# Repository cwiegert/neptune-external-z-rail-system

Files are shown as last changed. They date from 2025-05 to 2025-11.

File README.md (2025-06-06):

# Neptune 4 Pro – Z Axis Linear Rail Mounting System
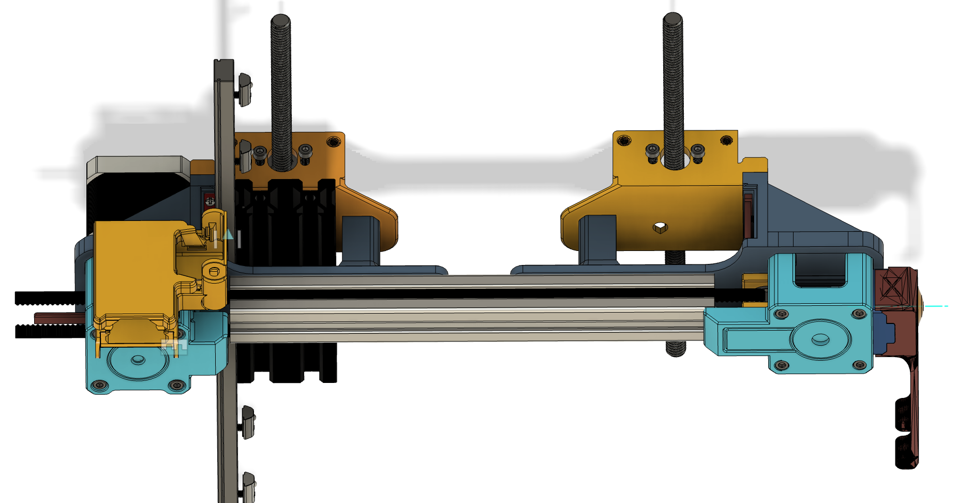
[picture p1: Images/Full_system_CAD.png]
Overview
 

This mod was inspired by the limitations and challenges imposed on Neptune printers by the TBStrong z rail kit.   Why do you need z rails at all?   Well, you don't, but I have them, and I never have to worry about aligning pom wheels, or any kind of z banding.   If you are here, you are interested in putting rails on the z axis, becuase you have probably already put the y axis rails and perhaps the x axis upgrade.    

This design incorporates rails on the outside of the Gantry.   Unlike the Tbstrong upgrade, this change will eliminate the interference with x axis movement and any cable chain system you might want to install.   The inside the gantry limits any well designed chain link system, as the adaptor off the tool head typically hits the rail on both gantry posts.

## 📦 Some basics to start wtih

- **This is an advanced mod and not something to be taking lightly.   Several different components are included in this modification and should only be done by someone with experience with complicated modifications**

- MGN12H rails are used, with the larger H carriages.

- Suggest to use light load Z rails, especially if you have a Beacon H or any other eddy probe. Any heavier preload will cause Z axis noise and cause the eddy to trigger early.

- There are prerequisites, you may want to consider. Initial release is designed to work with the SilencedFrost X axis rail upgrade  and the Layer.Shifted double shear X motor upgrade. 

- While changing the mount, consider an upgrade to a 48mm motor, over the 39mm on the stock Neptune 4 Pro.   The standard motor will work but if you are already doing this set of advanced modifications the motor upgrade is a nice add on

- All files have included in this repo which were sourced from other mods, have been modified to work for this kit.   Including the printhead hanger for the x axis rail modification and modded to support the end stop switch being flipped from stock, requireing a  finger on top of the rail to activate the end switch

- The current offset on the x axis endstop switch is designed to fit the stock position, and the finger added to the x axis printhead will trigger a stock -8.5mm
- **If you are using a tensioner idler pulley larger than a Gates Spec, be sure to print the Large profile tensioner housing**

## 🧰 Tools Required

- A working printer
- Hex drivers 2.5 and 2.0
- Soldering Iron (insert ends optional but recommended)

## 🛠️ Installation Overview

| Step | Instruction | Image |
|---|---|---|
| 1 | **Print the STL files** using your Neptune 4 Pro or another 3D printer. | |
| 2 | **Disassemble** the original Z-axis lead screw carriage if necessary. This is self-explanatory, and there are no parts from the stock Z-axis hardware that are reused except for the limit switch. | |
| 3 |  Add a M3x8 socket head screw to the rails, starting with the top and bottom, every other hole, and start a roll in t-nut to the rail |  |
| 4 |  Using the bearing keeper from the tools, remove the carraiges from the linear rail by holding the keeper tight to the rail, and slowly sliding the carriages onto the bearing keeper | |
| 5 | **Mount the linear rail** to the Z gantry. Use the `20x20x20` spacer block from the STL directory to position the 330mm rail. Tighten one rail screw, place the block on top, and align to the top of the gantry extrusion (with the top rail removed). This will give about 5mm of carriage travel before hitting the bed. Snap the MGN12H alingment tool to the bottom of the rail and align the rail to the center of the extrusion. Tighten the bottom screw tight enough to hold the rail. Move the alignment clip between the top 2 holes of the rail, loosen the top screw, snap the alignment rail to the extrusion and tighten the top screw just past finger tight.  , tighten them just past finger tight, moving the alignment jig up the rail as you go. **DO NOT ADD THE CARRIAGES YET** — you will lose bearings if you try to install the assembly all at once. | Step 3 |
| 6 | Run the belt through the tensioner pulley and set the tensioner on the x extrusion. It will register into the slides. | |
| 7 | Snap the double shear cap and the tensioner cover into the X extrusion bracket. The covers are designed to snap into the pockets on the x extrusion brackets and slide into the extrusion ends. You need to assemble the double shear bearing holder and the tensioner covers onto the x extrusion holders before assembling onto the Z rails. There will be no way to slide the ends into the 2020 extrusion once the X extrusion brackets are mounted on the 2020.  | |
| 8 | **Assemble the X-axis extrusion**. The X-axis brackets are designed for 2020 extrusion and not the stock one. The bracket mounting holes won’t align with stock extrusion holes. A future mod may support this. Using 2 M4x10 button head screws and M4 roll in t-nuts, mount the X brackets to the extrusion. Roughly align the carraige hanger portion of the bracket with the outside of the gantry rails.  Lower the assembly onto the gantry uprights, using the X-axis leveling jigs to maintain a level x axis. Leave all X extrusion screws loose for now, they will be tighten after step 7 | Step 4  Step 6|
| 9 | **Attach the carriage.** With the X extrusion in place, slide the carriages onto the rails and into the hangers. Mount them to the X-axis bracket with 4× M3x8mm flat head screws. Slide the X axis up/down a few times. Then:<br>&nbsp;&nbsp;&nbsp;&nbsp;1. Tighten the top rail screw.<br>&nbsp;&nbsp;&nbsp;&nbsp;2. Loosen other screws<br>&nbsp;&nbsp;&nbsp;&nbsp;3. Slide the X axis up and down again<br>&nbsp;&nbsp;&nbsp;&nbsp;4. Rest the X extrusion on the leveling blocks<br>&nbsp;&nbsp;&nbsp;&nbsp;5. Tighten screw nearest to X-axis on both rails<br>&nbsp;&nbsp;&nbsp;&nbsp;6. Slide the X extrusion to bottom of the rails<br>&nbsp;&nbsp;&nbsp;&nbsp;7. Tighten bottom screws<br>&nbsp;&nbsp;&nbsp;&nbsp;8. Finish by tightening remaining screws<br><br><br> At this point the carraige and the rails should be aligned and parallel to each other and the x extrusion should move freely with little to no friction |  Step 5 |
| 10 | **Tighten the X extrusion hangers**. Tighten the visible M4 screw in the X extrusion bracket using the access hole in the lead screw hanger. Remove the assembly from the gantry to access and tighten the hidden screw. Using the method described in step 4 **REMOVE THE CARRIAGES AGAIN**, repeat step 7 exactly. <br><br>Your motion system should now be aligned and level. | Step 6 |
| 11 | **Mount assembly to the lead screw nuts**. Whether using stock nuts or Oldhams, attach the lead screws. If using stock nuts: leave screws loose. If using Oldhams: tighten fully. | Step 7 |
| 12 | Slide the Printhead hanger onto the front rail. Again, you will need to upgrade to the SilencedFrost front rail hanger system, or use a top rail from the TbStrong X axis rail system to use this upgrade.  There is no adapatation to the stock Neptune 4 Pro x extrusion. Have not tested with the other Neptune 4 series. |  |
| 13 | Slide the motor into the receiver on the left side of the gantry. The motor should be difficult to slide into the receiver, and best to slide the outside into the holder, then push the back of the motor towards the linear rail carraige | |
| 14 | Follow the assembly instructions from the Layer.shifted double shear block, to mount the bearing into the holder, and the end stop into the cap of the double shear holder |  |
| 15 | Slide your belt pulley onto the belt, leave the grub nut loose.  Pressure fit the double shear pulley assembly onto the motor hanger, and add the end stop mount to the assembly by inserting the 4 screws and start them into the motor. Don't tighten them yet, just finger tight to hold the assembly together| |
| 16 |  Insert the pulley preload tool between the belt pulley and bearing of the double shear motor mount. This tool aligns the pulley with the center of the x axis extrusion and gives enough standoff to avoid rubbing on the shaft reinforcement bearing. |  |
| 17 |  Assemble the tensioner by adding the heat insert and the M3x45mm screw to the back of the tensioner | |
| 18 |  Assemble the idler pulley in the tensioner using the M5x20mm dowel. **If you are not using a Gates spec pulley, use the Large profile tensioner housing **  The tensioner slide will allow for 22mm dowel if you have 1 left over from another mod | |
| 19 | run the belt around the 2 pulleys and  making sure the tensioner pulley is onto the belt the correct way. You will need to make sure the belt is around the tensioner pulley before mounting the pulley to the cover. |  |
| 20 | Slide the tensioner into the tensioner cover, and pressure fit the tensioner cover to the x axis mount adn tighten the 4 M3x35 socket head screws  |  |
| 21 | If you are using the c270 camera holer, add the mounting block prior to adding the tensioner nob. There is no permanent mounting assembly for the block, it is loose fitting and held by the tension of the tensioner knob. The teardop around the mounting hole will register into the profile on the end of the tensioner cover. Add either the stock or the included tensioner knob and tighten slightly |  |
| 22 |  Tighten the belt to the print head hanger and assembly | |
| 23 |  Add the print head, and tune. Tension the x belt to the appropriate tension (roughly 130 HZ for sock length Neptune 4 Pro)

## 📌 Compatibility

- **Printer:** Elegoo Neptune 4 Pro, will likely work on all Neptune versions, but not tested.   If not using a X axis endstop, the Motor side double shear cover would not be needed
- **X Axis and extrusion** currently only supported on a X rail upgrade from @SilencedFrost as referenced in the BOM above
- **X Axis motor and motion**  requires the Lamarc double shear upgrade.   It may be compatible with stock limit switch and cover, but not tested
- **Rail type:** MGN12H (or similar) with 330mm recommended length.  .step files provided to invite mods for longer x extrusions and mods like purge buckets outside the print area
- **Clearances:** Designed to maintain compatibility with stock frame dimensions.  

## 🧪 Notes

- **IMPORTANT** Files are designed with **tight tolerances** to minimize backlash and reduce resonance vibrations
- .step files are included so you can modify dimensions or hole patterns as needed
- Be sure to tune your flow and PA, there are very tight tollerances designed into the parts, and there will be no design to relax the tollerances
- Supports are built in, and desinged to be break-away after cooling.   Difficult to remove supports with hot/warm part
- ASA-CF does not seem to hold up to screw pressure to well.   As the screw head puts pressure on the assembly, the ASA catestophically fails and splits the parts.   PETG-GF can be used as alternative where screw pressure causes ASA to fail
- Socket head screws used where over tightening will not cause splitting

## 📦 BOM
<small>
  
| Item| Part Description | Quantity | Source/Link | Notes |
|-----|---|---|---|---|
| 1 | MGN12H Linear Rail (330mm) | 2 | [Amazon](https://www.amazon.com/dp/B07Z5NKF42) | Light preload recommended |
| 2 | M3 x 8mm socket Head Screws | 16 | [Amazon](https://www.amazon.com/dp/B07CJ9BRCK?ref_=ppx_hzsearch_conn_dt_b_fed_asin_title_6&th=1) | required for mounting the rails and a number of the printed components |
| 3 | M3 x 6 Flat head Screws | 8 | [Amazon](https://www.amazon.com/dp/B0CG9K1NDX?ref_=ppx_hzsearch_conn_dt_b_fed_asin_title_2) | Mounting the carraiges to the X axis brackets |
| 4 | M3 x 8mm Button Head Screws | 4 | [Amazon](https://www.amazon.com/dp/B083HD61FV) | Mounting Lead screw hanger to the X axis bracket |
| 5 | Gates Powergrip® 2GT Toothed Idler 20T | 1 | [PrintedSolid](https://www.printedsolid.com/products/gates-powergrip-2gt-toothed-idler-5mm-id?variant=21236971241557) |  upgraded to a gates spec on the X axis idler |
| 6 | M3 x L4 x D4.2 Heat Insert  | 10 |  [Amazon](https://www.amazon.com/dp/B0BBSLL6G7)  |  These are the small heat inserts
| 7 | M3 x L4 x D5 Heat Insert | 6 | [Amazon](https://www.amazon.com/dp/B0CS6VZYL8) |  used for the heavier holding joints|
| 8 | M3 x 25 Socket Head Screw  |  2 |[Amazon](https://www.amazon.com/dp/B07NSX12DP) |  mounting the tensioner cover to the X mounting bracket|
| 9 | M3 x 40 Socket Head Screw  | 4  |  [Amazon](https://www.amazon.com/dp/B0D5CQ5SX3)  | mounting the double shear cover to the base and motor. Purchased a bundle instead of all independent  |
| 10 | M3 x 45 Flat Head Screw | 1 | [Amazon](https://www.amazon.com/iexcell-Thread-Stainless-Socket-Screws/dp/B0CR6F4FQ2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) | mounting the tensioner knob |
| 10  | M6 Gates GT2 belt | 1  | [Amazon](https://www.amazon.com/dp/B08R93QQ8Z)  | new belt for futre extension of x axis length  |
| 11  | M5 x 20 steel Dowel  | 1 | [Amazon](https://www.amazon.com/dp/B07MB8QMT8)  | for the idler pulley  |
| 12  | M3 Spring T Nut 2020 | 14  | [Amazon](https://www.amazon.com/dp/B09H5B17GT)  | mounting the rails |
| 13  | M4 Roll in T-Nut with Ball Spring| 4  | [Amazon](https://www.amazon.com/dp/B0D12GMX2Y)  |  mounting to the X extrusion  |
| 14  | 48mm Stepper Motor (optional) | 1 | [Moons Upgrade](https://www.aliexpress.us/item/3256805046302407.html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) | This is not mandatory, but why go through all the upgrading and not upgrade the base motor |
| 15 | SilencedFrost X-Axis Rail Upgrade | 1 | [Github](https://github.com/SilencedFrost/Neptune-4-series-X-rail) | Supporting Parts, Printhead back from here |
| 16 | Layer.Shifted X-Motor Double Shear Mount | 1 | [Printables](https://www.printables.com/model/1222791-neptune-44pro-x-axis-double-shear-motor-upgrade) | Source for some of the base files, remix included in this repo|
| 17 | X axis extrusion leveler | 1 | [Printables](https://www.printables.com/model/680531-elegoo-neptune-4-pro-gantry-level/files)|Source files for the x axis levelers|
| 18 | Carriage block assembly helper | 2 | [Printables](https://www.printables.com/model/118195-mgn9-mgn12-blockcarriage-disassembly-helpers)| Source for bearing keeper|

</small>

## 🛠️ Printing suggestions
- 0.4mm nozzle
- ASA-CF, PETG-GF, ASA or more rigid filaments.
- 0.2 layer height
- 0.45 layer width
- no supports, all necessary supports are built in
- Lead screw hangers printed with lead screw hole on build plate
- Double Shear parts printed with "cap" on plate - all parts with largest flat surface on plate
- Tensioner knob - not necessary, but included as a longer knob portion to account for camera hanger knob lock

## 🛠️ Modifications Ecouraged
- The step files are included to encourage creativity and modificaitons.   This is a starter pack and framework designed and implemented on a Neptune 4 Pro
- If you have suggestions, please add an issue, and I will consider adding the additions as user modifications.
- After enough beta testing, will consider making kit available on Printables.

## 🤝 Contributing

Improvements, remixes, or support for other printers are welcome!
Feel free to fork the repo and submit pull requests.

## 📜 License

This project is open source and licensed under the [MIT License](LICENSE).

## 🙌 Acknowledgments

Inspired by community mods for the Neptune and Ender series printers.

---

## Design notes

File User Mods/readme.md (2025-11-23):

## Folder Structure:
* / files / mod_for / mod_name / STLs /
* / files / mod_for / mod_name / CAD /
* / files / mod_for / mod_name / Images /
* / files / mod_for / mod_name / README.md

### Notes:
* README.md - Include some help for others that want to use your mod. Pictures/BOM/build notes etc.
* Images - Pictures and videos you embed in your README.md and any other pictures that may be helpful.
* CAD - Help encourage others to build on your creation. Include your CAD files here.
* STLs - Put all the required STLs here. Try to make them ready for printing. Correctly orientated and with no mesh errors etc.

In the [/files](files) folder there is another README.md file that has a table/index to list of all the usermods. When you add yours, update that table with information about your mod so that everyone can find your awesome or atrocious work.

## [Show me the mods already!](files/README.md)

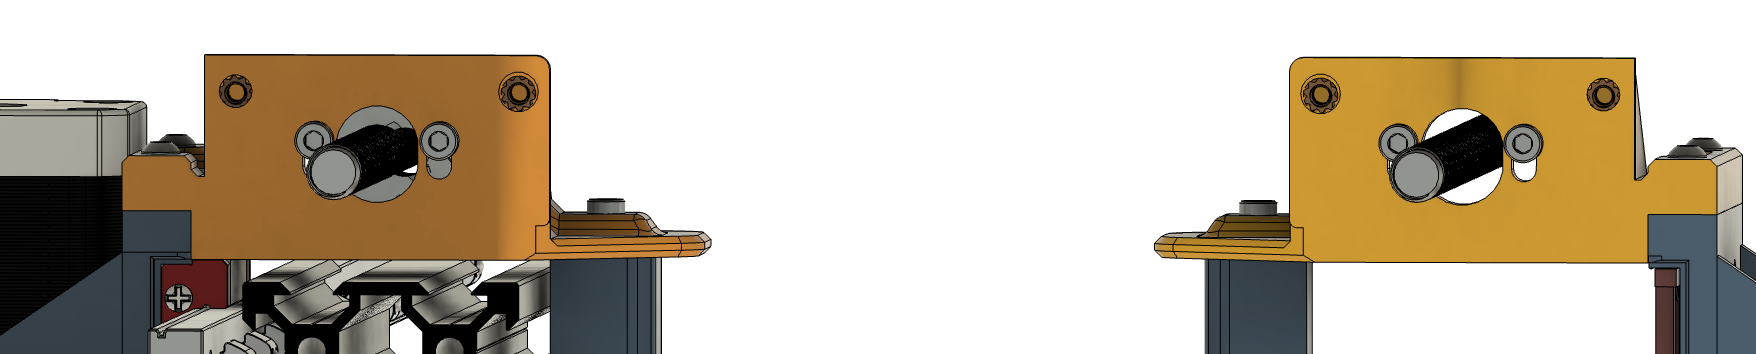
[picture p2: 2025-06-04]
Images/Lead_Screw_Hangers_CAD.png

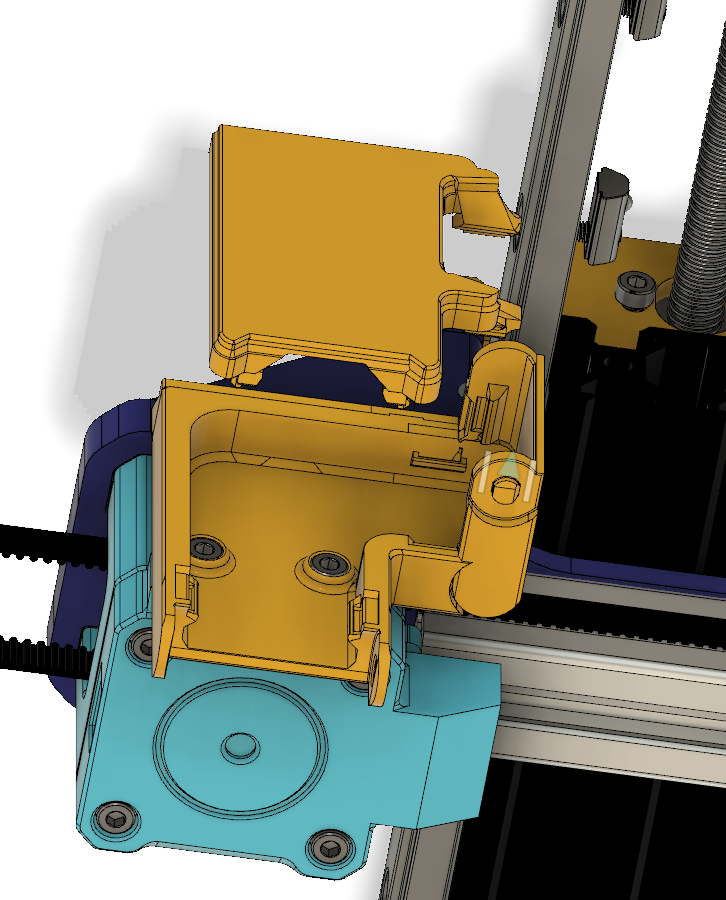
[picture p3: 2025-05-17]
Images/Chain_transition_mount .png

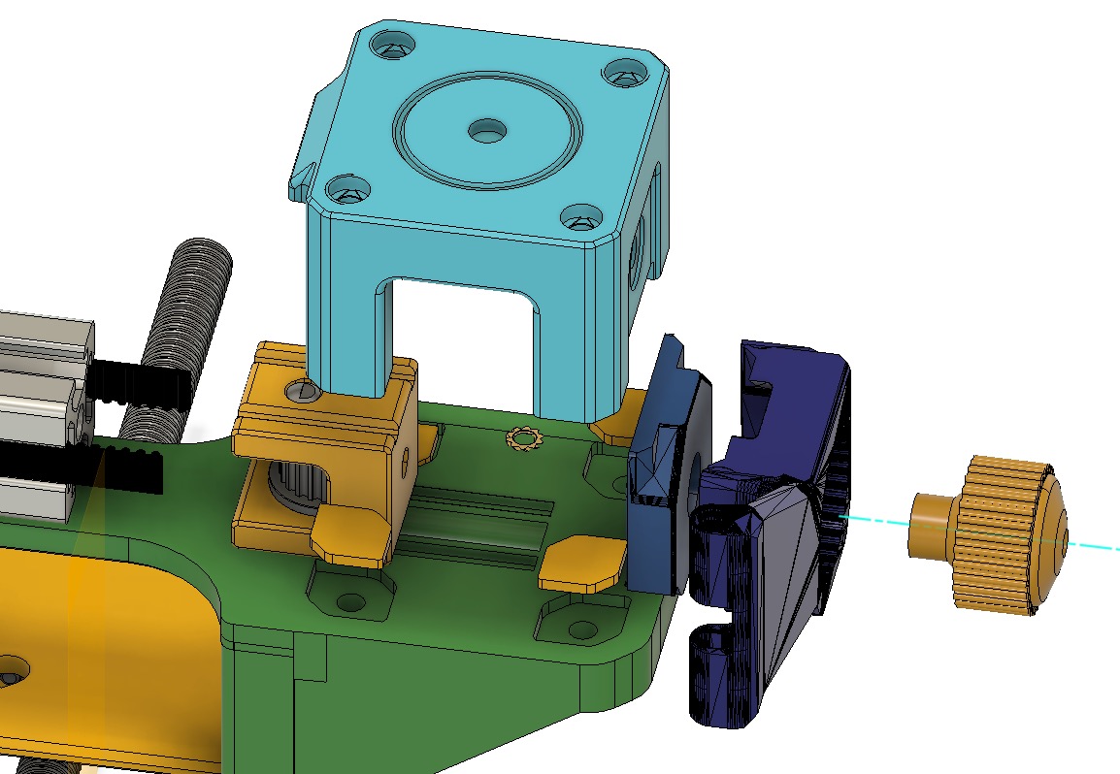
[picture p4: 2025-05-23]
Images/Tensioner side part expansion.jpeg

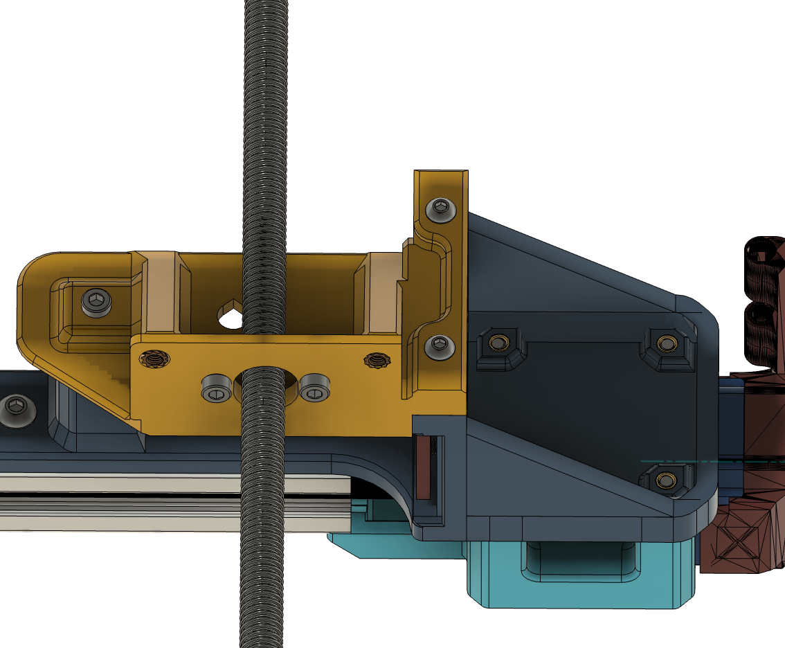
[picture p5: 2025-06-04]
Images/Lead_Screw_hanger_Tension_CAD.png

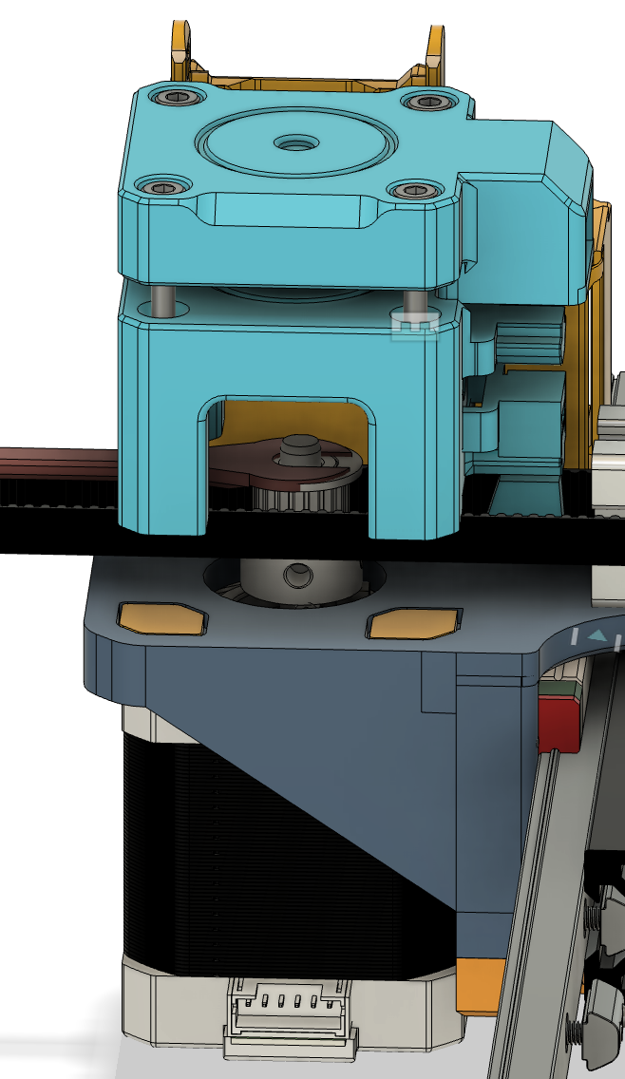
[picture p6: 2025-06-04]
Images/Motor_Side_doubleShear_exploded.png

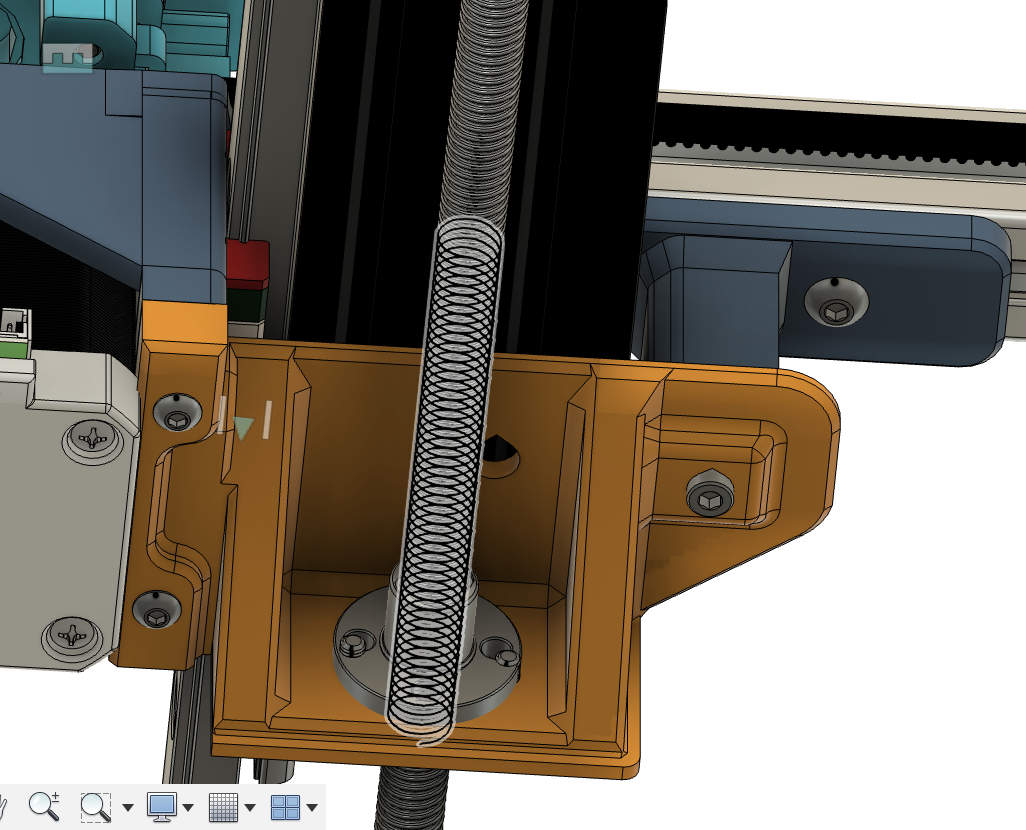
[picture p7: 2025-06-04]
Images/Lead_Screw_closeup_CAD.png

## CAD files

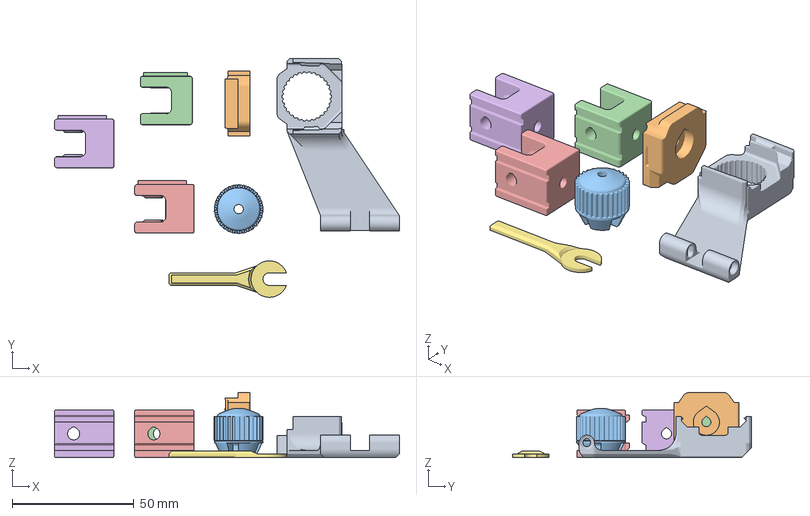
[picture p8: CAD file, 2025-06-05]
3mf files/WoodWorker z rail misc parts.3mf
141.9 x 98.1 x 26.8 mm
LS_xAxisBeltTensioner_c270_n4pro_v09.stl
101d8807-47bf-4285-90e4-e2f9bfa1ebe2.stl
Tensioner knob v16.stl
Body2.stl
Body1.stl x 3

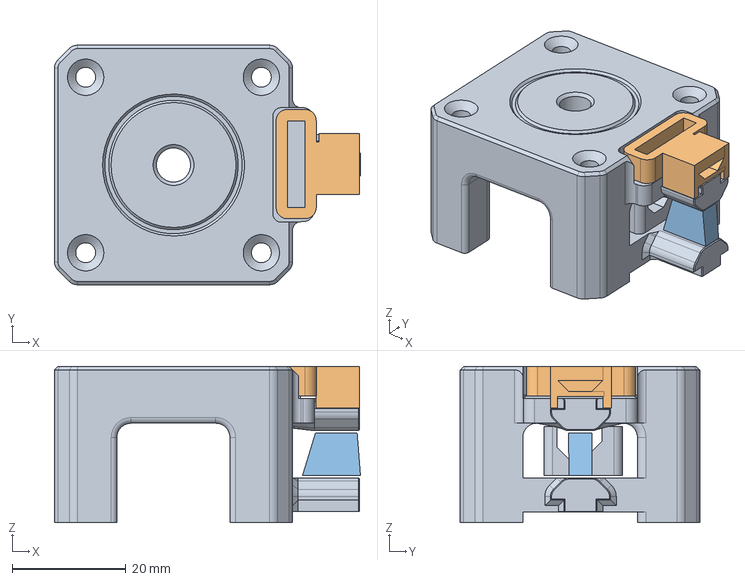
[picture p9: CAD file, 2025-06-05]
Step Files/Larmarc Mod/WoodWorker - remix of Lamarc double shear Bearing Body.step
53.9 x 42.2 x 27.5 mm

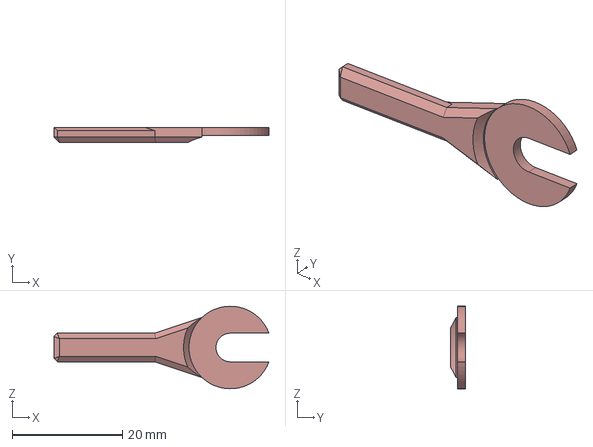
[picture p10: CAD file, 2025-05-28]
Step Files/Motor Pulley Preload Jig.step
39.1 x 2.75 x 15.0 mm

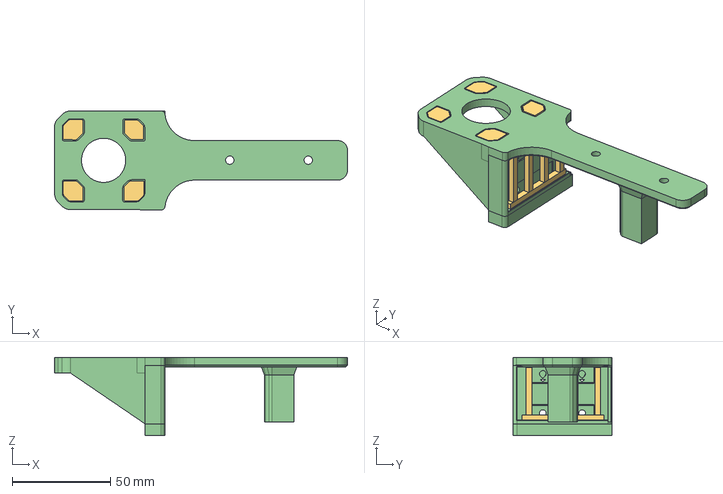
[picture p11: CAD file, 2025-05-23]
Step Files/Motor Side/WoodWorker - X Axis Mount outside Rail.step
149.4 x 50.5 x 40.0 mm

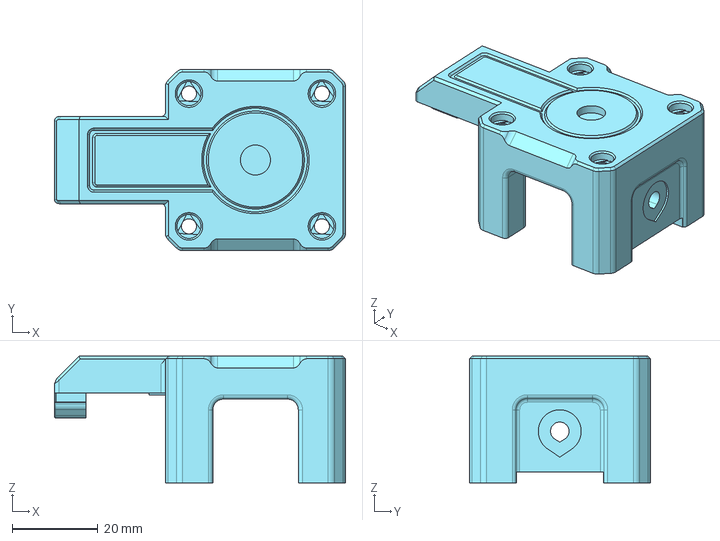
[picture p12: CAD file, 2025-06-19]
Step Files/Tensioner side/Woodworker N4Pro Double Shear Tensioner cover.step
67.8 x 42.2 x 29.5 mm

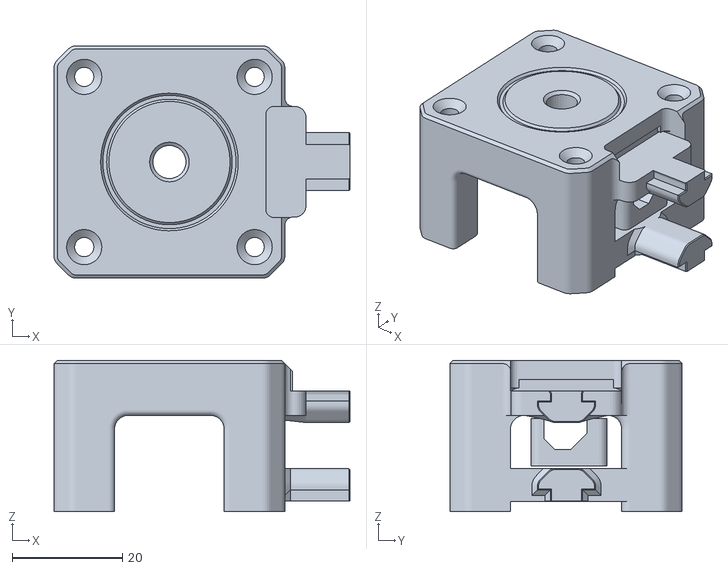
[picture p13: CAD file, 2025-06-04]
STLs/Lamarc Double Shear Mod/WoodWorker - Lamarc N4Pro Double Shear Bearing holder - Z Rail hangers.stl
53.8 x 42.2 x 27.5

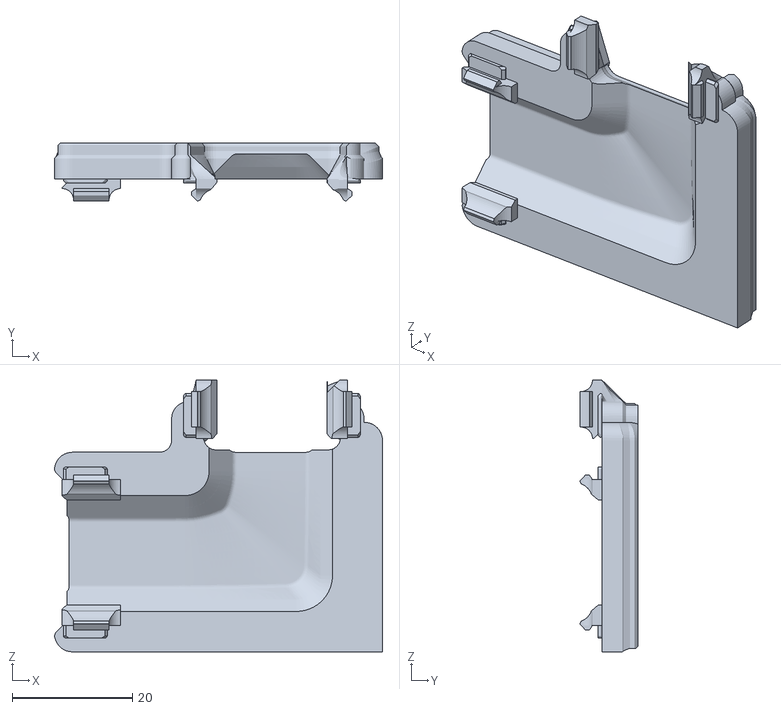
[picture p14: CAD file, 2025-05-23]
STLs/Motor Side/WoodWorker - Lamarc chain Z Gantry Rail Corner Cver.stl
54.5 x 9.70 x 45.1

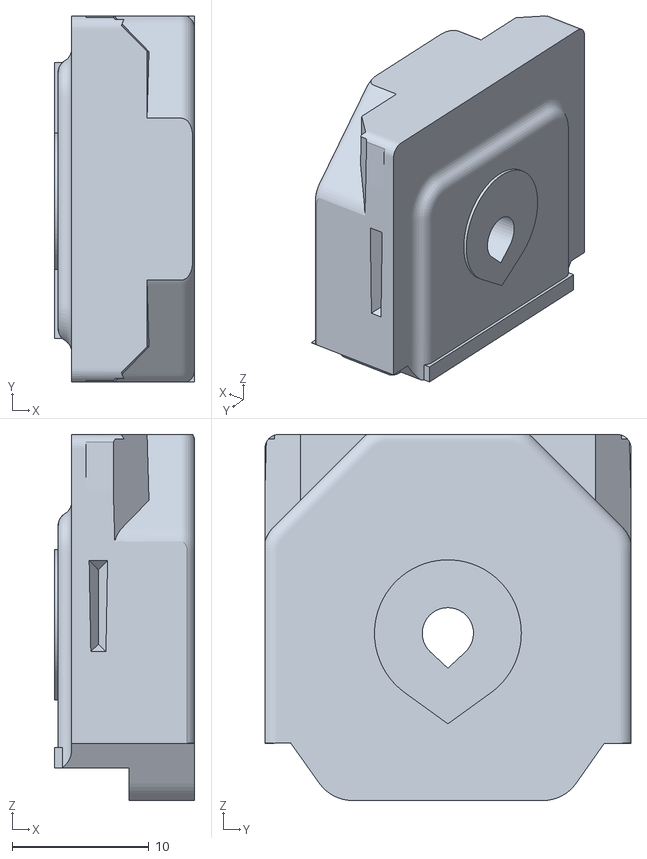
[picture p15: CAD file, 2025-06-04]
STLs/Tensioner Side/WoodWorker - Tensioner side mounting block for Camera.stl
10.3 x 26.8 x 26.8

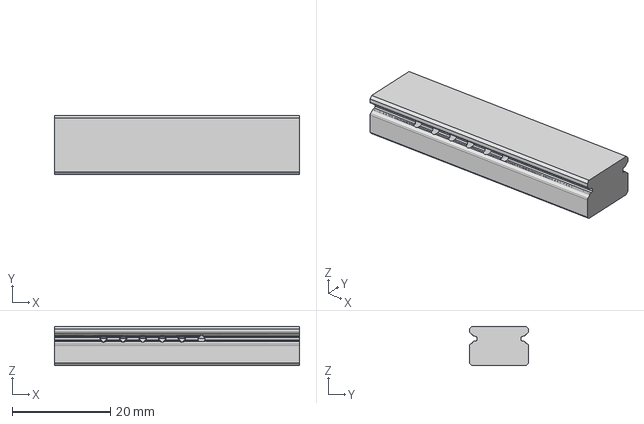
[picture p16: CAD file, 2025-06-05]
Tools/MGN12H- Bearing Keeper v1.step
50.0 x 12.0 x 8.00 mm

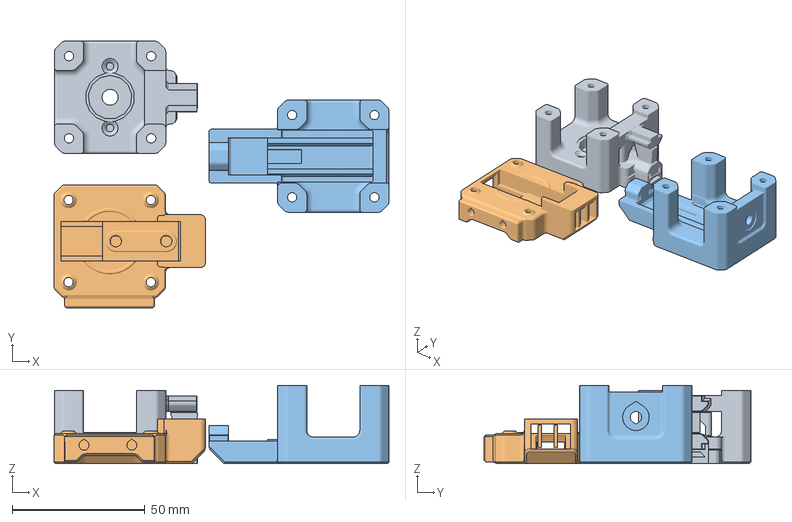
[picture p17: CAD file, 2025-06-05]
3mf files/WoodWorker N4Pro double Shear covers for z rails mod.3mf
126.1 x 100.4 x 29.5 mm
Lamarc N4Pro Double Shear Limit.stl
Lamarc N4Pro Double Shear Limit (1).stl
Woodworker N4Pro Double Shear Tensioner.stl

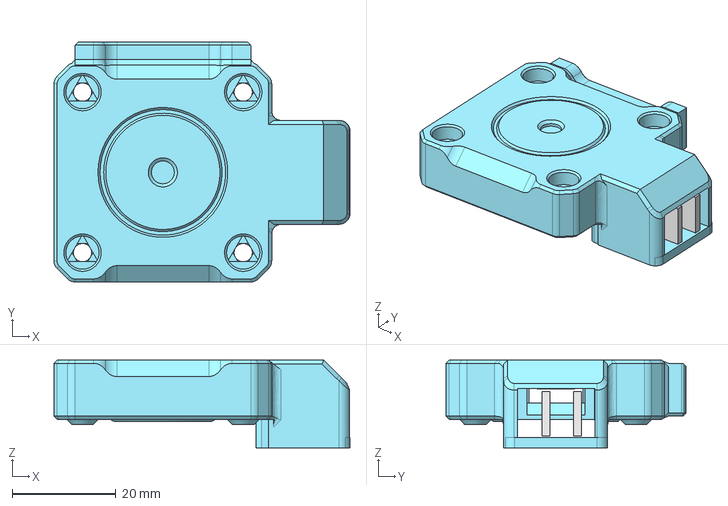
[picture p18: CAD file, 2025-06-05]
Step Files/Larmarc Mod/WoodWorker - remix of Lamarc double shear Limit Switch cover v61.step
57.0 x 46.2 x 16.9 mm

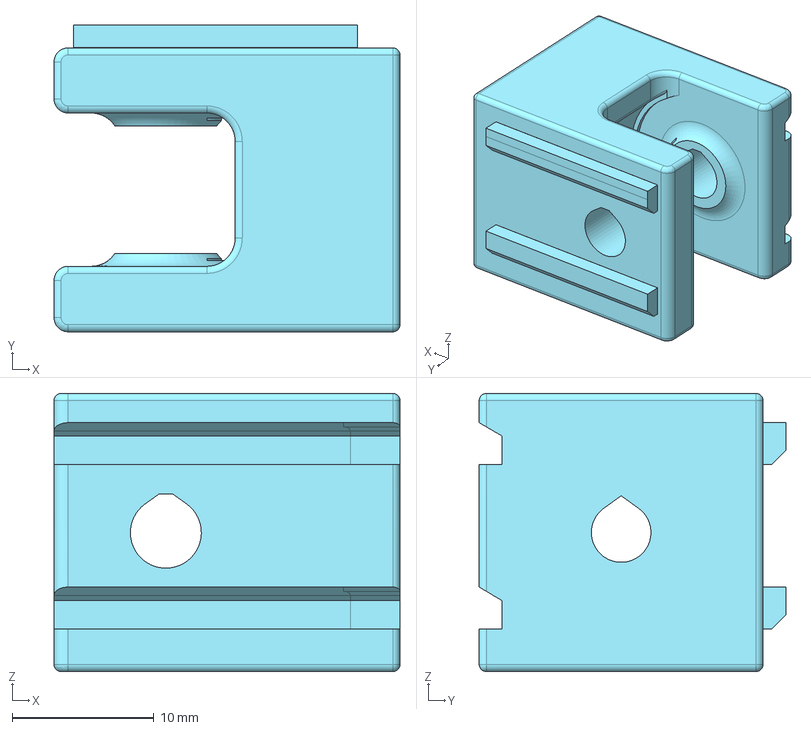
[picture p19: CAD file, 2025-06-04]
Step Files/Tensioner side/WoodWorker New X Tensioner - Medium Profile.step
24.4 x 21.6 x 19.6 mm

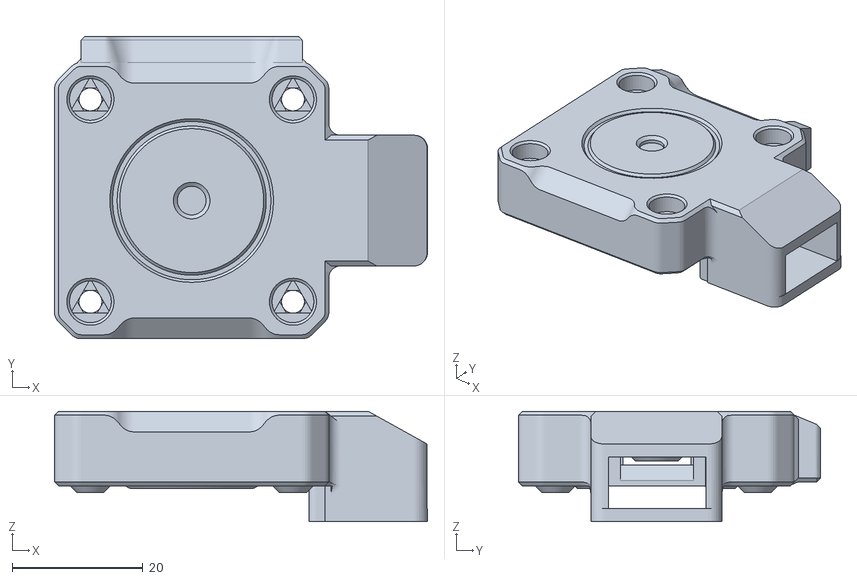
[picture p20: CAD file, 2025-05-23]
STLs/Lamarc Double Shear Mod/WoodWorker -Lamarc N4Pro Double Shear Limit Stock.stl
57.0 x 46.2 x 16.9

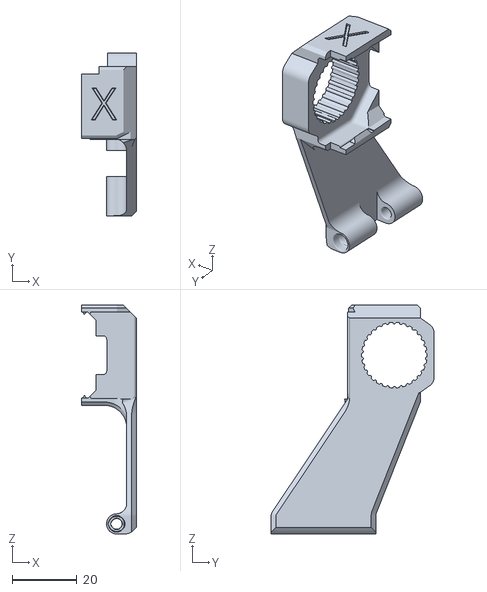
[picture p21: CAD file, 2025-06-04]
STLs/Tensioner Side/WoodWorkeer - LS_xAxisBeltTensioner_c270_n4pro_v09.stl
17.0 x 50.4 x 70.8

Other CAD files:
Tools/MGN12H Bearing Keeper.stl
3mf files/WoodWorker X and Z hangers.3mf
Step Files/Tensioner side/WoodWorker - New X Tensioner - Large Profile.step
STLs/Motor Side/WoodWorker - Lamarc chain corner - front of gantry.stl
STLs/Motor Side/WoodWorker - Lead Screw mounting plate Motor side.stl
STLs/Motor Side/WoodWorker - x Axis extrusion Mount.stl
STLs/Tensioner Side/WoodWorker - Lead Screw mounting plate Tensioner side.stl
STLs/Tensioner Side/WoodWorker - Tensioner knob v16.stl
STLs/Tensioner Side/WoodWorker - X axis tensioner - Large gear.stl
STLs/Tensioner Side/WoodWorker New X Tensioner - Gates Gear.stl
STLs/Tensioner Side/WoodWorker Symetry - Tensioner side X extrusion mount.stl
STLs/Tensioner Side/Woodworker - New X Tensioner - Large Profile.stl
STLs/Tensioner Side/Woodworker N4Pro Double Shear Tensioner cover.stl
Step Files/Motor Side/WoodWorker - Motor Side Lead Screw Hanger.step
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

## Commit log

2025-05-17 initial build
    step and STLS for the z rail mounting system
    [Lamarc N4Pro Double Shear Limit Body - WoodWorker remix.step.stl, Lamarc N4Pro Double Shear Limit Cover - WoodWorker remix Z Rail.stl, Lamarc N4Pro Double Shea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]
2025-05-18 updated to let carraiges slide in
    [Main Corner Body For Z Axis outside Gantry.step, Motor Side x Rail Bracket.step, Tensioner Side X Rail Mount.step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]
2025-05-18 fixing repo
    moving files around, making sure to segment the parts included from other original designs
    [Lamarc N4Pro Double Shear Limit Body - WoodWorker remix.step.stl, Lamarc N4Pro Double Shear Limit Cover - WoodWorker remix Z Rail.stl, Lamarc N4Pro Double Shea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]
2025-05-18 cleaning up duplicates in step directory
    [WoodWorker - Motor Side Lead Screw mounting bracket.step, WoodWorker - Tensioner side Lead screw mounting bracket.step]
2025-05-18 Cleaning up STL directory
    [WoodWorker - Motor Side Lead Screw mounting bracket.stl, WoodWorker - Tensioner side Lead screw mounting bracket.stl]
2025-05-19 updated place of lead screw hole
    [WoodWorker - Motor Side Lead Screw Hanger.step, WoodWorker - Motor Side X rail mount.step, WoodWorker - Motor Side X rail mount.stl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]
2025-05-23 Final release of .stls
    Finished modeling, testing and ready to release for testing
    [Lamarc N4Pro Double Shear Limit Body - WoodWorker remix.step.stl, Lamarc N4Pro Double Shear Limit Cover - WoodWorker remix Z Rail.stl, Lamarc N4Pro Double Shea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]
2025-05-23 adding camera hanger
2025-05-23 Create WoodWorkeer - LS_xAxisBeltTensioner_c270_n4pro_v09.stl
    [WoodWorkeer - LS_xAxisBeltTensioner_c270_n4pro_v09.stl]
2025-05-23 fixed tensioner side mount
    [WoodWorker - Symetry Tensioner side X extrusion mount.stl, Woodworker N4Pro Double Shear Tensioner cover.stl, Woodworker N4Pro Double Shear Tensioner.stl]
2025-05-23 Create WoodWorker -Lamarc N4Pro Double Shear Limit Stock.stl
    [WoodWorker -Lamarc N4Pro Double Shear Limit Stock.stl]
2025-05-23 updated step files
    [Tensioner Cover with adaptor for lamarc camera hanger.step, Tensioner Cover with adaptor for lamarc camera hanger.stl]
2025-05-23 from the laptop
    [Lamarc N4Pro Double Shear Limit Cover - WoodWorker remix.step, Lamarc N4Pro Double Shear Limit.step, Main Corner Body For Z Axis outside Gantry.step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]
2025-05-23 Create WoodWorker - X Axis Mount outside Rail.step
    [WoodWorker - X Axis Mount outside Rail.step]
2025-05-23 reorganizing directory and file structure
    [Tensioner Cover with adaptor for lamarc camera hanger.step, WoodWorker - Tensioner Side Lead Screw Hanger.step]
2025-05-23 removing duplicate files
    [WoodWorker -Lamarc N4Pro Double Shear Limit Stock.stl]
2025-05-23 remove old camera knob lock
    [WoodWorker - LS_xAxisBeltTensioner_c270_n4pro_v09.stl]
2025-05-25 Added the Large adn Medium profile tensioners
    The original tensioner is made to fit a gates spec, during testing, a 18mm outer ring pulley was used, and testing with a 16 mm showed there should be 3 size tensioners
    [WoodWorker - New X Tensioner - Large Profile.step, WoodWorker - New X Tensioner - Large Profile.stl, WoodWorker - New X Tensioner - Medium Profile.step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]
2025-05-25 Fixed the tensioner side 22 mm dowel slot
    Cleaned up the time line, redid the tensioner dowel slot, added a chamfer brace to inside edge of tensioner cover hanger
    [WoodWorker - Symetry - Tensioner side X Extrusion mount.step, WoodWorker - Symetry Tensioner side X extrusion mount.stl, WoodWorker Symetry - Tensioner side X 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]
2025-05-26 cleaning up step files and STL's
    [Tensioner Cover with adaptor for lamarc camera hanger.step, Tensioner Cover with adaptor for lamarc camera hanger.stl, WoodWorker - New X Tensioner - Large Pro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]
2025-05-27 tensioner cover
    [WoodWorker - Lamarc N4Pro Double Shear Bearing holder - Z Rail hangers.stl, Woodworker N4Pro Double Shear Tensioner cover.stl]
2025-05-28 last tensioner cover addition
2025-05-28 Added preload Jig and rail mounting spacer
    [Motor Pulley Preload Jig.step, Motor Pulley Preload Jig.stl, Rail Mounting Spacer.stl]
2025-05-29 Ready to release for testing
    [WoodWorkeer - LS_xAxisBeltTensioner_c270_n4pro_v09.stl, WoodWorker - Lamarc N4Pro Double Shear Bearing holder - Z Rail hangers.stl, WoodWorker - Remix of Lamar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]
2025-06-04 added Tools directory and updated latest files
    [2020_12mm_linear_rail_alignment_clip.stl, Motor Pulley Preload Jig.stl, Tensioner knob v16.stl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]
2025-06-04 fixing tensioner file names
    [Tensioner knob v16.stl, WoodWorker - Tensioner side mounting block for Camera.stl, WoodWorker - X axis tensioner - Large gear.stl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]
2025-06-04 Updating the camera mounting block
    The tear drop was pointing the wrong direction for the register on the tensioner cover
    [WoodWorker - Tensioner side mounting block for Camera.stl]
2025-06-05 change the limit switch end
2025-06-05 zipped up the step files
    [WoodWorker - Remix of Lamarc N4Pro Double Shear Limit.step, WoodWorker - remix of Lamarc double shear Limit Switch cover.step]
2025-06-05 adding 3MF's and pictures
    [WoodWorker N4Pro double Shear covers for z rails mod.3mf, WoodWorker X and Z hangers.3mf, WoodWorker z rail misc parts.3mf]
2025-06-05 Added Bearing keepers to tools directory
    [MGN12H Bearing Keeper.stl, MGN12H- Bearing Keeper v1.step]
2025-06-05 fixed Lamarc Step Files
    [WoodWorker - Tensioner Housing remixed from double shear.step, WoodWorker - remix of Lamarc double shear Bearing Body.step, WoodWorker - remix of Lamarc double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]
2025-06-09 updated tensioner cover to fix screw hole
    [WoodWorker - Tensioner Housing remixed from double shear.step, Woodworker N4Pro Double Shear Tensioner cover.stl]
2025-06-18 updated tensioner cover
    [WoodWorker - Tensioner Housing remixed from double shear.step, WoodWorker - x Axis extrusion Mount.stl, Woodworker N4Pro Double Shear Tensioner cover.step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]
2025-06-19 fixed slide on tensioner cover
    [WoodWorker - New X Tensioner - Large Profile.stl, Woodworker N4Pro Double Shear Tensioner cover.step, Woodworker N4Pro Double Shear Tensioner cover.stl]
